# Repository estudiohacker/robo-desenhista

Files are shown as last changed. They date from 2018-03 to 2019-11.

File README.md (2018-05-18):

Projeto de um robô desenhista por [Monica Rizzolli](https://github.com/MonicaRizzolli/) e [João Adriano Freitas](https://github.com/jaafreitas/). Inspirado no [Open Source Turtle Robot ](https://github.com/aspro648/OSTR) por MakersBox.

[Vídeo demonstração](https://youtu.be/GalOWkOCb_o)

Ilustrações: Monica Rizzolli

## Lista de materiais

* 2 motores de passo 28BYJ-48 5VDC

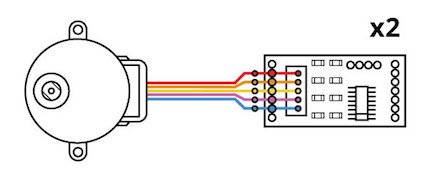
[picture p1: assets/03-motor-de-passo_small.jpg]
3-motor-de-passo_small
   

* 1 micro servo 9g SG90

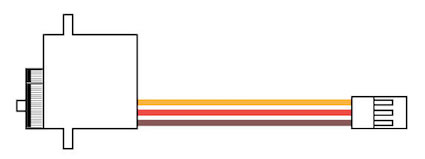
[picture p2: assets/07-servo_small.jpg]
7-serv
   

* 1 Arduino Nano

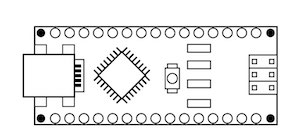
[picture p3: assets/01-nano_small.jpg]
1-nano_smal
   

* 1 Placa Shield de Expansão para Arduino Nano

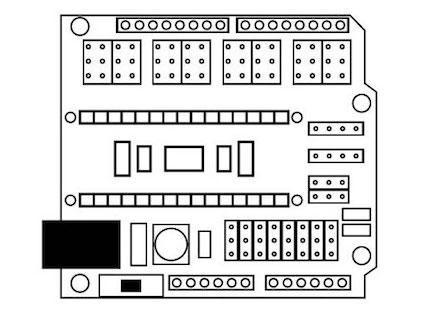
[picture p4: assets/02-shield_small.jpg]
2-shield_smal
   

* 1 Cabo USB compatível com o Arduino Nano

* 12 Jumpers fêmea-fêmea

   0-jumpers_femea_femea_smal
   
* 14 porcas fêmeas hexagonal M3
* 18 parafusos Allen M3x8
* 14 parafusos cabeça redonda M2.5x8
* 1 bola de metal 5/8"
* 2 anéis de borracha (O-ring) 1 7/8" x 1/8"

## Montagem eletrônica
* Micro servo na porta digital 2: fio laranja no S, vermlho no V e marrom no G

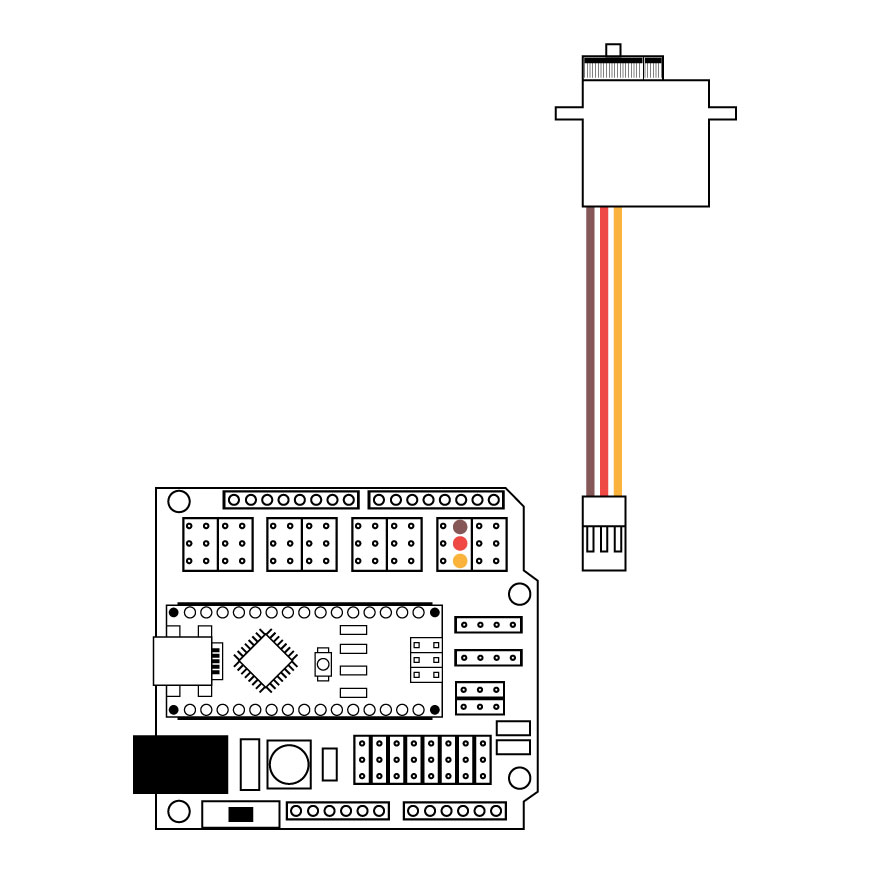
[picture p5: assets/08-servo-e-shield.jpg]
8-servo-e-shield
  

* Motor de passo da direita: pino digital S 4 no IN1, S 5 no IN2, S 6 no IN3 e S 7 no IN4. Alimentação 4 V no + e 4 G no -.

* Motor de passo da esquerda: pino digital S 8 no IN1, S 9 no IN2, S 10 no IN3 e S 11 no IN4. Alimentação 8 V no + e 4 G no -.

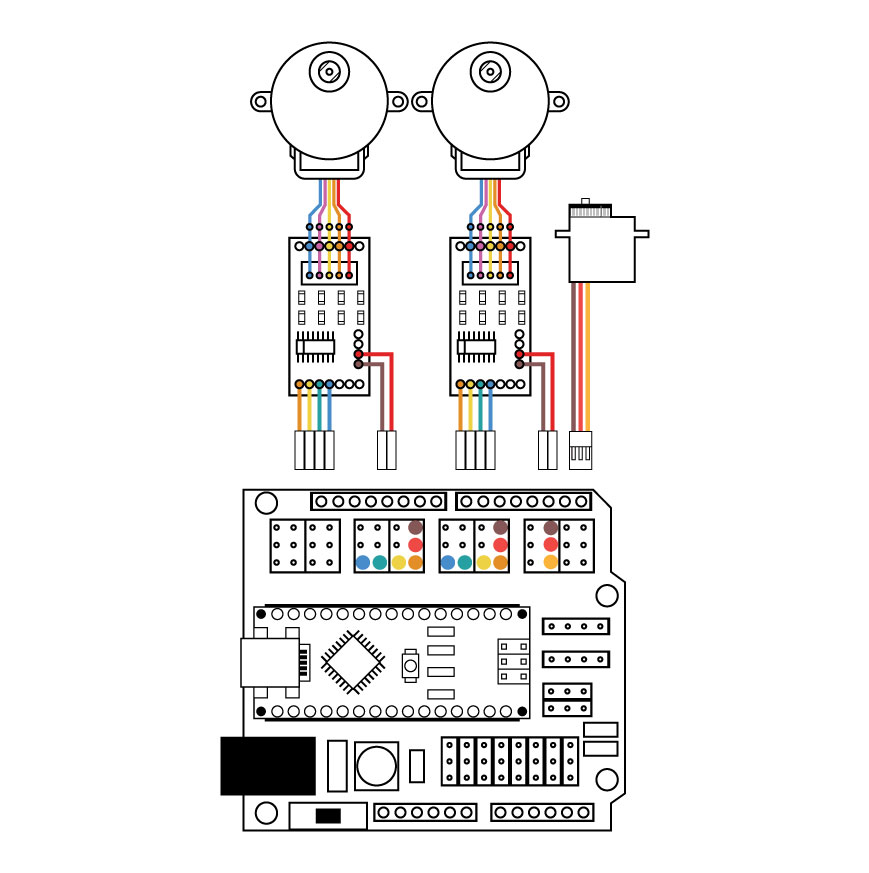
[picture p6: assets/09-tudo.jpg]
9-tud


## Licença
[Attribution-ShareAlike 3.0 United States (CC BY-SA 3.0 US)](https://creativecommons.org/licenses/by-sa/3.0/us/)

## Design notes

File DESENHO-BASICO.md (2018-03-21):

## Desenho Básico

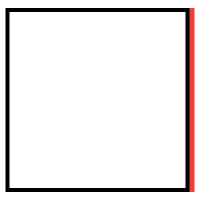
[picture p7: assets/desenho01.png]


```C
for (var count = 0; count < 4; count++){
  moveForward(100); // tamanho do lado do quadrado
  turnRight(90);
}
``` 

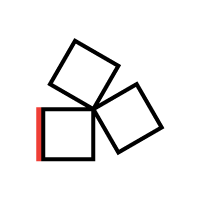
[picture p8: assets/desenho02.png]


```C
// nesse loop definimos quantas vezes o quadrado será desenhado - 3 nesse caso
for (var count1 = 0; count1 < 3; count1++){ 
  // nesse loop desenhamos os lados do quadrado
  for (var count = 0; count < 4; count++){ 
    moveForward(100); // definir o tamanho do lado do quadrado
    turnRight(90);
  }
  // aqui definimos quantos graus o quadrado deve rotacionar. 
  // para descobrir o ângulo, dividimos 360 pela quantidade de vezes que o quadrado é desenhado
  // nesse caso 360/3 = 120
  turnRight(120);
}
``` 

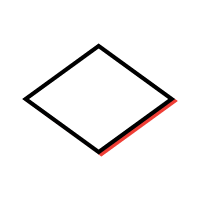
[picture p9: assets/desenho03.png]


```C
for (var count = 0; count < 2; count++){
  moveForward(100); // tamanho do lado do losango
  turnRight(60);
  moveForward(100); // tamanho do lado do losango
  turnRight(120);
}
```

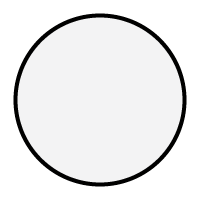
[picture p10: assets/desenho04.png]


```C
for (var count = 0; count < 360; count++){
  moveForward(1);
  turnRight(1);
}
```

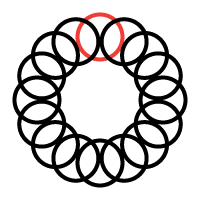
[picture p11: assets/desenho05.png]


```C
// nesse loop definimos quantas vezes o círculo será desenhado - 16 nesse caso
for (var count1 = 0; count1 < 16; count1++){
  // desenhar o círculo
  for (var count = 0; count < 360; count++){
    moveForward(1);
    turnRight(1);
  }
  jumpForward(50); // testar outros valores
  // para descobrir o ângulo, dividimos 360 pela quantidade de vezes que o quadrado é desenhado
  // nesse caso 360/16 = 22.5
  turnRight(22.5);
}
``` 

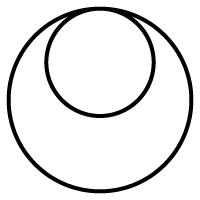
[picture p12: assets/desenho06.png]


```C
// círculo menor
for (var count = 0; count < 36; count++){
  moveForward(5);
  turnRight(10);
}

//círculo maior
for (var count = 0; count < 36; count++){
  moveForward(10);
  turnRight(10);
}
```

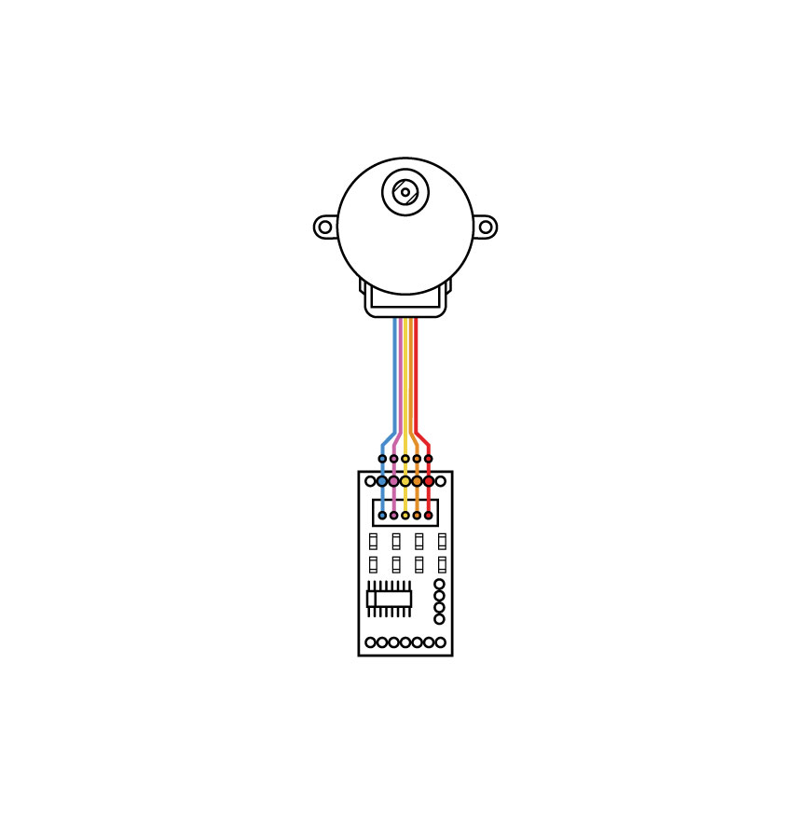
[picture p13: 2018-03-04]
assets/03-motor-de-passo.jpg

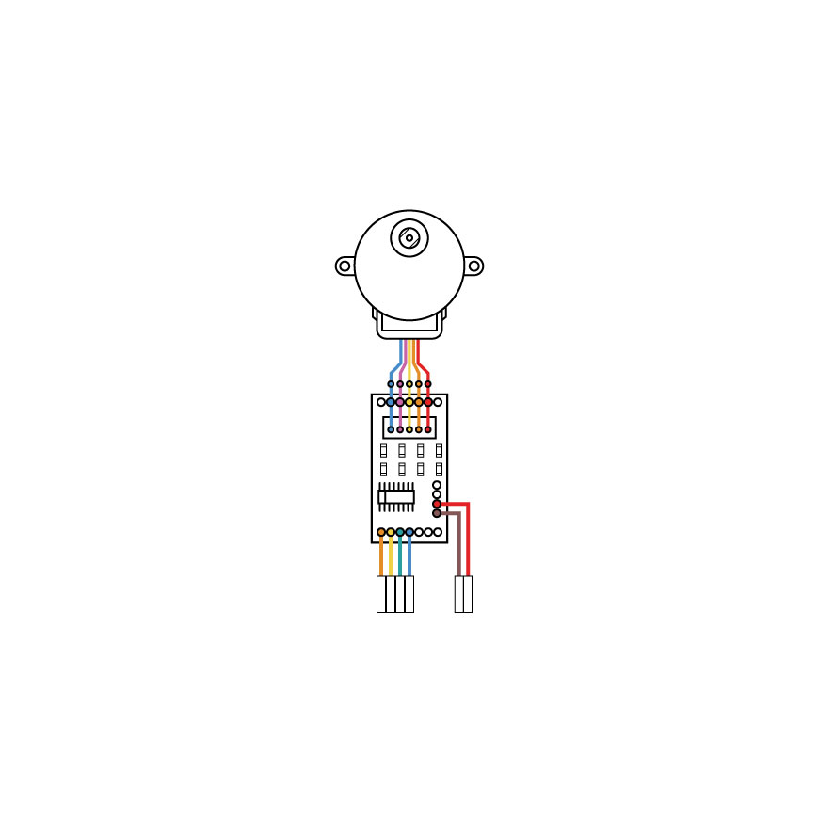
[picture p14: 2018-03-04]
assets/04-passo-com-cabos.jpg

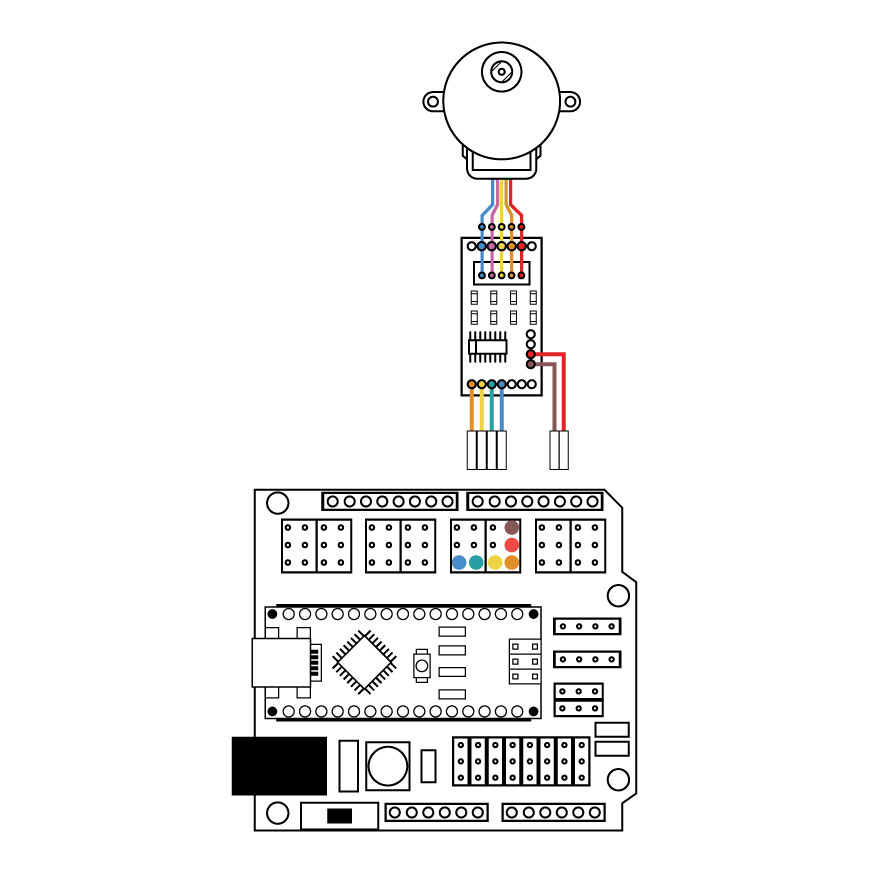
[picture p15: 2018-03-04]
assets/05-passo-com-shield.jpg

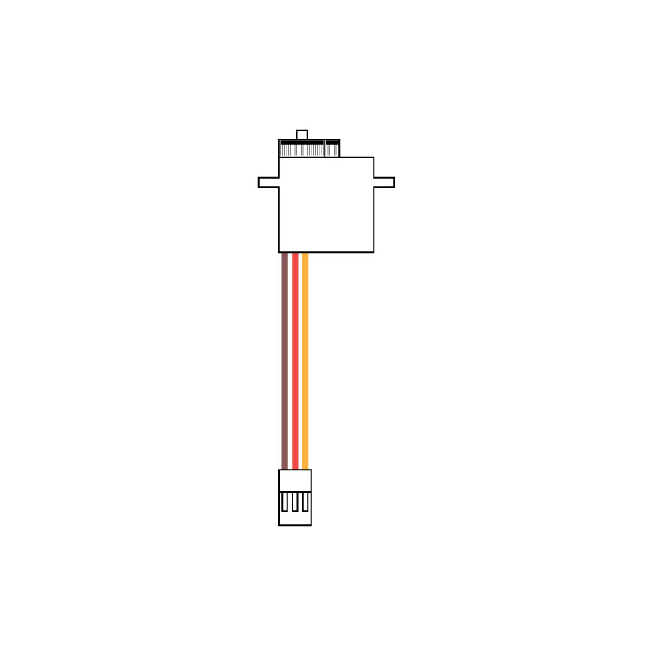
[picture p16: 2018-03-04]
assets/07-servo.jpg

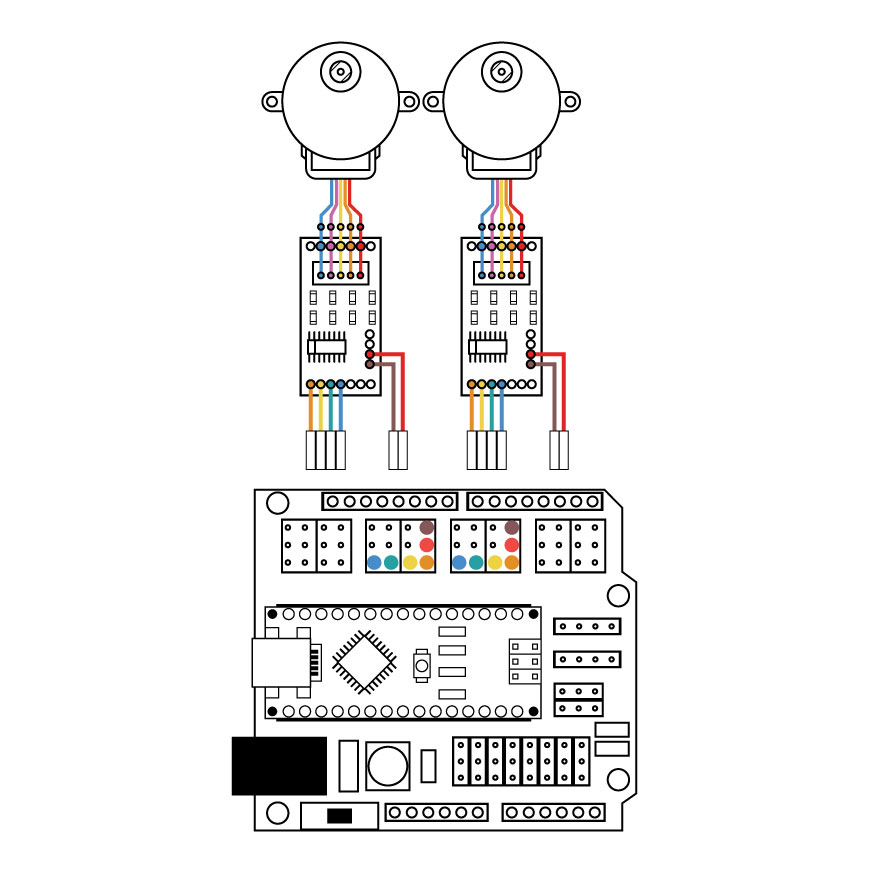
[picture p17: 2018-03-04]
assets/06-dois-motores.jpg

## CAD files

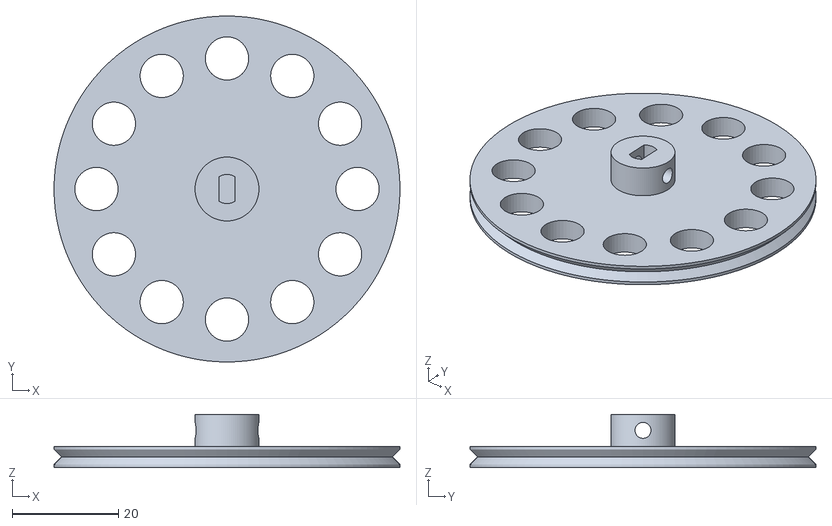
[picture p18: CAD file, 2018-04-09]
modelo/Wheel.stl
65.0 x 65.0 x 10.0

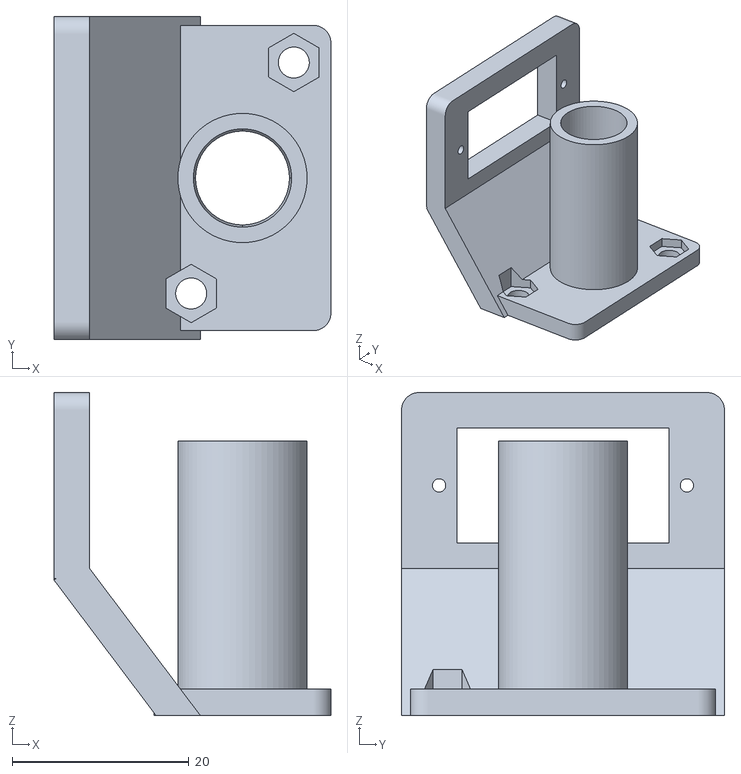
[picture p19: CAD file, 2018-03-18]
modelo/Pen_Holder2_edited.stl
31.3 x 36.5 x 36.5

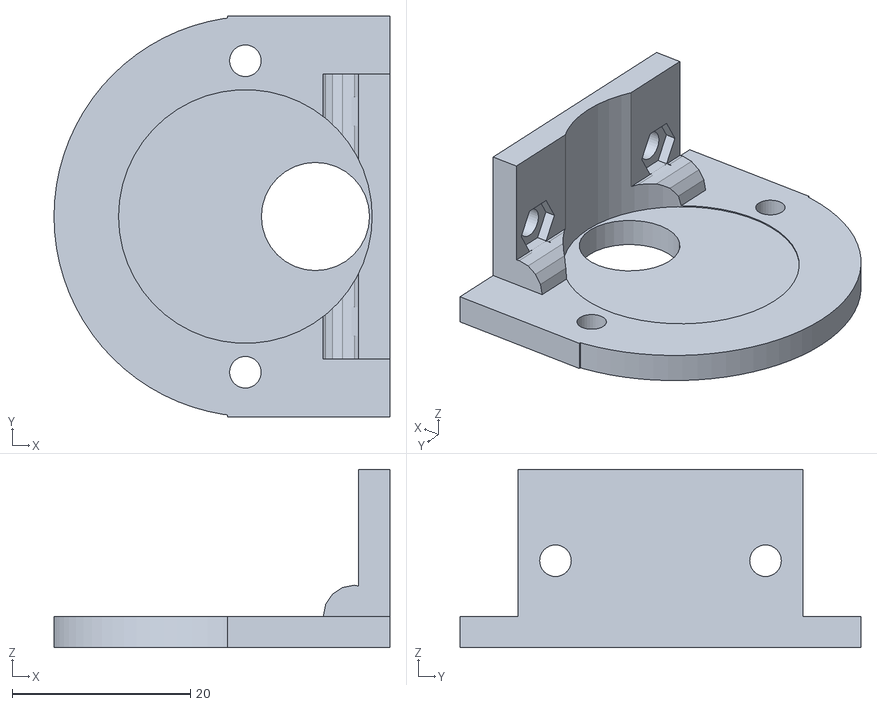
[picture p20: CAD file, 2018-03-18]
modelo/Stepper_Bracket2.stl
37.8 x 45.0 x 20.0

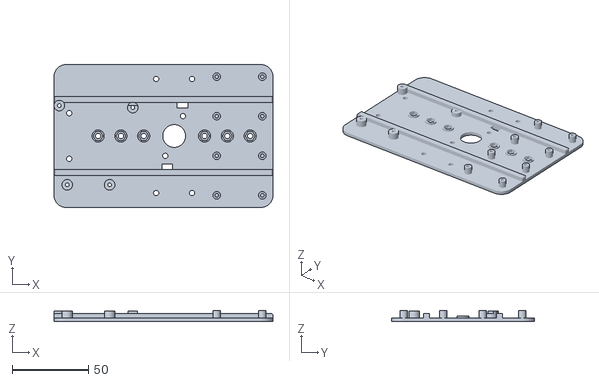
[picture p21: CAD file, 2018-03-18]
modelo/Chassis_Arduino2-modules.stl
144.0 x 94.0 x 7.40

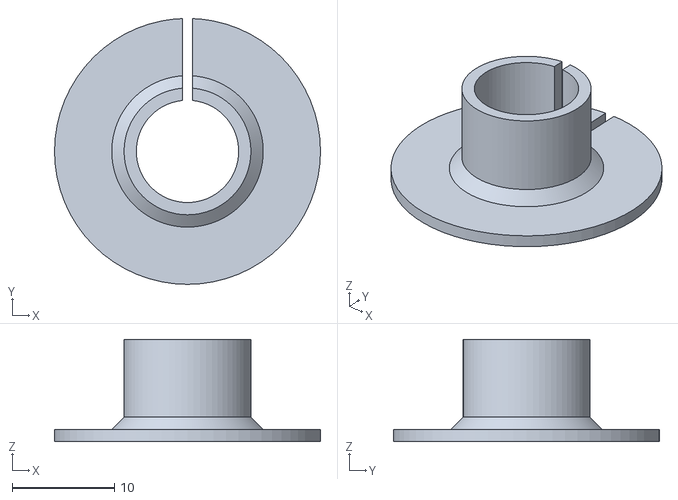
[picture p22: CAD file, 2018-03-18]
modelo/Pen_Collar2.stl
26.0 x 26.0 x 10.0

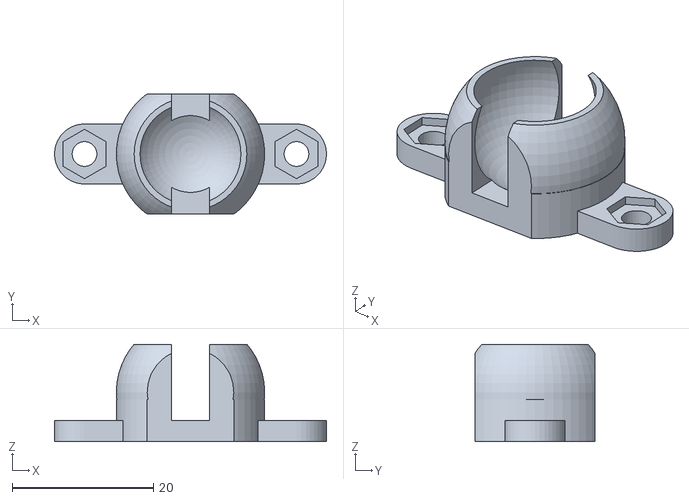
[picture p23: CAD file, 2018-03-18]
modelo/Caster2.stl
38.5 x 17.0 x 13.8

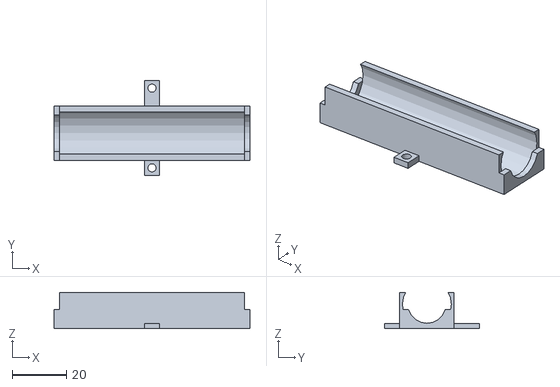
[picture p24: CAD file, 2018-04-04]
modelo/18650 battery holder.stl
72.0 x 34.8 x 13.4

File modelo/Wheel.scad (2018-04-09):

// Original script by Mark Benson
// http://www.thingverse.com/thing:122070
// 23/07/2013

// Wheel for maze mouse
// Shaft fitting for 28BYJ-48 geared stepper

// Modified by 648.ken@gmail.com Jun 2015
// Lengthened hub
// increased shaft cutout
// Included M3 set screw hole (might need to be tapped)
// Added parameters for customizer

// Creative commons non commercial


// http://www.thingiverse.com/thing:16193/
use <write/Write.scad>


/* [Global] */
features = "spokes"; // [spokes, plain, hub-only]

/* [Wheel] */
// Diameter of wheel in mm.
wheel_diameter = 65;

// Increase shaft cutout size in mm if your printer is not calibrated.
fudge_factor = 0;

/* [Text] */

// You will have to flip it around to see it. 
text = "Estudio Hacker";

// Font selection
font = "orbitron.dxf";

// 8mm goes all the way through, but may cause trouble with letters like "B".
letter_depth = 2; // [0:8]

// Letter spacing
letter_spacing = 1.3; 

// Letter height in mm.
letter_height = 6.8;


difference(){
	union()	{
		//rim
        if (features != "hub-only"){
            cylinder(r=wheel_diameter / 2, h=4, $fn=100);
        }

		//boss
		cylinder(r=12 / 2, h=10, $fn=100);
	}


	union()	{
		//shaft cutout (shaft with flat)
		translate([0, 0, 0.6])
		intersection(){
			cylinder(r=5.5 / 2 + fudge_factor, h=12, $fn=40); // was 5
			translate([0, 0, 4]) cube([3.0 + fudge_factor, 12, 12], 
                                       center=true); // was 2.5
		}

		// set screw for M3
		translate([0, 0, 7])		
		rotate([90, 0, 90])
		cylinder(r=1.5, h=60, center=true, $fn=40); // was 1

		//rim groove cutout
		translate([0, 0, 2])
		rotate_extrude(convexity=10, $fn=100)
		translate([wheel_diameter / 2, 0, 10])
		rotate([0,0,45])
		square([2,2],center=true);

        // add text to face
        if(letter_depth > 0){
            rotate(180, [1, 0, 0]){
                writecircle(text, [0, 0, 0], 
                            wheel_diameter / 3.1 - letter_height, 
                            font=font, space=letter_spacing, 
                            t=letter_depth, h=letter_height);
            }
        }
        // add spokes (circular cut-outs)        
        if (features == "spokes"){
            for(i = [0:11]){
                rotate(i * 360 / 12, [0, 0, 1])
                translate([wheel_diameter / 2.75, 0, -1])
                cylinder(r=wheel_diameter / 16, h=8, $fn=40);
            }
        }
	}
}

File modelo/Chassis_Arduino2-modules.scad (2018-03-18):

$fn = 64;


baseThickness = 2.4;
cornerRounding = 8;
plateOffset = 7;    // shift entire plate on x axis
railOffset = 16;     // plate lenght - railLength
M3holeDia = 3.5;
M3nutDia = 6.5;
holeOffset = M3holeDia * 1.2;
batteryOffset = 20;

cassis_wid = 94; // 94 for full Raspberry Pi, 84 for A+ ?
cassis_len = 144;

xArduinoOffset = 20;
yArduinoOffset = -4;

penDiameter = 15.0;
penRadius = penDiameter / 2;
baseLen = 34.5;
baseWid = 20;

railWidth = 4;

cutout_len = 45;
cutout_wid = 15;

difference(){
    
    union(){
        // cassis plate
        translate([-cassis_len / 2 - plateOffset, -cassis_wid / 2, 0])
        roundedCube(cassis_len, cassis_wid, baseThickness, cornerRounding);
        
        // rail
        translate([-cassis_len / 2 - plateOffset, 
                   cassis_wid / 2 - 25 + railWidth, baseThickness / 2])
            rotate([90, 0, 0])    
            roundedCube(cassis_len, 4, railWidth, 1);
        
        //rail
        translate([-cassis_len / 2 - plateOffset, 
                   -cassis_wid / 2 + 25, baseThickness / 2])
            rotate([90, 0, 0])    
            roundedCube(cassis_len, 4, railWidth, 1); 
     
        // Arduino mount standoffs
        rotate([0, 0, -90])
        translate([-40, -74, 0])
        union(){


        // Arduino mounts lower left (power jack)
        translate([xArduinoOffset, yArduinoOffset + 2.5, 0])
        color("lightblue")
        cylinder(standoffThickness, standoffDia / 2, standoffDia / 2);

        // upper left (USB)
        translate([xArduinoOffset + 1.3, yArduinoOffset+ (53.3 - 2.5), 0])
        color("lightblue")
        cylinder(standoffThickness, standoffDia / 2, standoffDia / 2);

        // upper right
        translate([xArduinoOffset + 1.3 + 50.8, yArduinoOffset +(53.3 - 2.5 - 15.2), 0])
        color("lightblue")
        cylinder(standoffThickness, standoffDia / 2, standoffDia / 2);

        // lower right
        translate([xArduinoOffset + 1.3 + 50.8, yArduinoOffset + (53.3 - 2.5 - 15.2 - 27.9), 0])
        color("lightblue")
        cylinder(standoffThickness, standoffDia / 2, standoffDia / 2);
        }
        
        //battery standoffs
        translate([batteryOffset, 0, baseThickness - 1])
        cylinder(baseThickness, d=standoffDia + 1, d=standoffDia + 1);  
        translate([batteryOffset + 15, 0, baseThickness - 1])
        cylinder(baseThickness, d=standoffDia + 1, d=standoffDia + 1);
        translate([batteryOffset + 30, 0, baseThickness - 1])
        cylinder(baseThickness, d=standoffDia + 1, d=standoffDia + 1);   

        translate([-batteryOffset, 0, baseThickness - 1])
        cylinder(baseThickness, d=standoffDia + 1, d=standoffDia + 1);  
        translate([-batteryOffset - 15, 0, baseThickness - 1])
        cylinder(baseThickness, d=standoffDia + 1, d=standoffDia + 1);
        translate([-batteryOffset - 30, 0, baseThickness - 1])
        cylinder(baseThickness, d=standoffDia + 1, d=standoffDia + 1);        
		
		// stepper board standoffs
 
		translate([batteryOffset+5, 12-8, baseThickness - 4])
			servo_board();
		translate([batteryOffset+5, -56+8, baseThickness - 4])
			servo_board();
    }

    // center pen hole
    cylinder(baseThickness, penRadius, penRadius);


    // pen holder bolt holes (low left, counter-clockwise)
    translate([-baseWid / 2 + holeOffset, -baseLen / 2 + holeOffset, 0])
    cylinder(baseThickness, d=M3holeDia, d=M3holeDia);
    
    /*
    translate([baseWid / 2 - holeOffset, -baseLen / 2 + holeOffset, 0])
    cylinder(baseThickness, d=M3holeDia, d=M3holeDia);
    */
    translate([baseWid / 2 - holeOffset, baseLen / 2 - holeOffset, 0])
    cylinder(baseThickness, d=M3holeDia, d=M3holeDia);
    /*
    translate([-baseWid / 2 + holeOffset, baseLen / 2 - holeOffset, 0])
    cylinder(baseThickness, d=M3holeDia, d=M3holeDia);
    */

    // bracket bolt holes
    bracketOffset = 9.5;
    translate([11.8, cassis_wid / 2 - bracketOffset, 0])
    cylinder(baseThickness, d=M3holeDia, d=M3holeDia);    

    translate([-11.8, cassis_wid / 2 - bracketOffset, 0])
    cylinder(baseThickness, d=M3holeDia, d=M3holeDia);    

    translate([11.8, -cassis_wid / 2 + bracketOffset, 0])
    cylinder(baseThickness, d=M3holeDia, d=M3holeDia);    

    translate([-11.8, -cassis_wid / 2 + bracketOffset, 0])
    cylinder(baseThickness, d=M3holeDia, d=M3holeDia);   


    // cable runs
    translate([2, 22 - M3holeDia, 0])
    cube([M3holeDia * 2, M3holeDia, baseThickness, ]); 

    translate([-8, -22, 0])
    cube([M3holeDia * 2, M3holeDia, baseThickness, ]); 
   
   
    // caster mount
    translate([-cassis_len / 2 + 10 - plateOffset, -15, 0])
    cylinder(baseThickness, d=M3holeDia, d=M3holeDia);     
    translate([-cassis_len / 2 + 10 - plateOffset, 15, 0])
    cylinder(baseThickness, d=M3holeDia, d=M3holeDia);    
  
    // battery holes
    translate([batteryOffset, 0, 0])
    cylinder(baseThickness, d=M3holeDia, d=M3holeDia);  
    translate([batteryOffset + 15, 0, 0])
    cylinder(baseThickness, d=M3holeDia, d=M3holeDia);
    translate([batteryOffset + 30, 0, 0])
    cylinder(baseThickness, d=M3holeDia, d=M3holeDia);   

    translate([-batteryOffset, 0, 0])
    cylinder(baseThickness, d=M3holeDia, d=M3holeDia);  
    translate([-batteryOffset - 15, 0, 0])
    cylinder(baseThickness, d=M3holeDia, d=M3holeDia);
    translate([-batteryOffset - 30, 0, 0])
    cylinder(baseThickness, d=M3holeDia, d=M3holeDia); 



    // battery nut nolders
    translate([batteryOffset, 0, baseThickness - 1])
    cylinder(baseThickness, d=M3nutDia, d=M3nutDia, $fn=6);
    translate([batteryOffset + 15, 0, baseThickness - 1])
    cylinder(baseThickness, d=M3nutDia, d=M3nutDia, $fn=6);
    translate([batteryOffset + 30, 0, baseThickness - 1])
    cylinder(baseThickness, d=M3nutDia, d=M3nutDia, $fn=6);   

    translate([-batteryOffset, 0, baseThickness - 1])
    cylinder(baseThickness, d=M3nutDia, d=M3nutDia, $fn=6);  
    translate([-batteryOffset - 15, 0, baseThickness - 1])
    cylinder(baseThickness, d=M3nutDia, d=M3nutDia, $fn=6);
    translate([-batteryOffset - 30, 0, baseThickness - 1])
    cylinder(baseThickness, d=M3nutDia, d=M3nutDia, $fn=6);



 
    // cutouts?
    /*
    translate([- cutout_len / 2 + 35, -cassis_wid / 2 + 25, 0])
    cube([cutout_len, cutout_wid, baseThickness]);
    translate([- cutout_len / 2 + 35, cassis_wid / 2 - 25 - cutout_wid, 0])
    cube([cutout_len, cutout_wid, baseThickness]);

    translate([-cutout_len / 2 - 35, -cassis_wid / 2 + 25, 0])
    cube([cutout_len, cutout_wid, baseThickness]);
    translate([- cutout_len / 2 - 35, cassis_wid / 2 - 25 - cutout_wid, 0])
    cube([cutout_len - 18, cutout_wid, baseThickness]);
    //translate([- cutout_len / 2 - 35, - cutout_wid / 2, 0])
    //cube([cutout_len, cutout_wid, baseThickness]);
    */


    // standoffs drills
    rotate([0, 0, -90])
    translate([-40, -74, 0])
    union(){
    // Arduino mounts lower left (power jack)
    translate([xArduinoOffset, yArduinoOffset + 2.5, 0])
    color("lightblue")
    cylinder(standoffThickness, standoffHoleDia / 2, standoffHoleDia / 2);

    // upper left (USB)
    translate([xArduinoOffset+ 1.3, yArduinoOffset + (53.3 - 2.5), 0])
    color("lightblue")
    cylinder(standoffThickness, standoffHoleDia / 2, standoffHoleDia / 2);

    // cutout for solder joints
    translate([xArduinoOffset+ 1.3 - 1.5, yArduinoOffset + (53.3 - 2.5) -standoffThickness / 2, 5.5])
    color("lightblue")
    cube(standoffThickness, standoffThickness, 8);


    // upper right
    translate([xArduinoOffset + 1.3 + 50.8 , yArduinoOffset + (53.3 - 2.5 - 15.2), 0])
    color("lightblue")
    cylinder(standoffThickness, standoffHoleDia / 2, standoffHoleDia / 2);

    // lower right
    translate([xArduinoOffset + 1.3 + 50.8, yArduinoOffset + (53.3 - 2.5 - 15.2 - 27.9), 0])
    color("lightblue")
    cylinder(standoffThickness, standoffHoleDia / 2, standoffHoleDia / 2);
    }

	
}

module stand_off()
{
    translate([0,0,-1])
    {
        difference() 
        {
            cylinder(h=5,d=5, center= false);
            cylinder(h=5,d=2.5, center= false);
        }
    }
}

module servo_board()
{
    translate([3,9,5]) stand_off();
    translate([3,35,5]) stand_off();
    translate([33,9,5]) stand_off();
    translate([33,35,5]) stand_off();
}

module roundedCube(xdim ,ydim ,zdim, rdim){
	hull(){ // https://youtu.be/gKOkJWiTgAY
		translate([rdim, rdim, 0]) cylinder(zdim, rdim, rdim);
		translate([xdim-rdim, rdim, 0]) cylinder(zdim, rdim, rdim);
		translate([rdim, ydim-rdim, 0]) cylinder(zdim, rdim, rdim);
		translate([xdim-rdim, ydim-rdim, 0]) cylinder(zdim, rdim, rdim);
	}
}

standoffDia = 7;
standoffThickness = 7;
standoffHoleDia = 2.5;


module Pi(){
    // Pi lower left 
    translate([3.5, 3.5, 0])
        color("pink")
        difference(){
            cylinder(standoffThickness, standoffDia / 2, standoffDia / 2);
            cylinder(standoffThickness, standoffHoleDia / 2, standoffHoleDia / 2);
        }
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

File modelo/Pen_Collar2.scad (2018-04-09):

// pen holder for plotting robot

$fn = 64;

// holder variables
penDiameter = 10; // 12.5mm works with Sharpie Fine
                  // 11.75 for Visa-vis
                  // 10 mm for Crayola Washables
                  // 8.3m para caneta hidrográfica lavável Happy-time (slice = 0).
penRadius = penDiameter / 2;
barrelHieght = 10;
barrelWallThickness = 3;
baseThickness = 3;
cornerRounding = 2;

hat_thickness = 1.2;

hatDiameter = 26;
slice = 1;


module penHolder(){

	difference(){
		//// lip
        cylinder(hat_thickness, hatDiameter / 2, hatDiameter / 2);
        
        // pen hole
        cylinder(baseThickness, penRadius, penRadius);
        

        // expansion slice
        translate([ -slice / 2, 0, 0])
        cube([  slice, hatDiameter, barrelHieght]);
	}

	// pen barrel
	difference(){
        // barrel

        barrel();

		// bore
		cylinder(   barrelHieght * 2, penRadius, penRadius);

        
        // expansion slice
        translate([ -slice / 2, 0, 0])
        cube([  slice, hatDiameter * 2, hatDiameter * 2]);   
	};  
}

module barrel()
        union(){{
		cylinder(	barrelHieght, 
					penRadius + hat_thickness, 
					penRadius + hat_thickness);


        rotate_extrude($fn=200)
        //rotate([90, 0, 0])
        translate([-penRadius - 2 * hat_thickness, hat_thickness, 0])
        polygon(points=[[2,2], [2,0], [0,0]]);
        }
    }
//barrel();
penHolder();

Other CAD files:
modelo/write/orbitron.dxf
modelo/Pen_Holder2_edited.scad
modelo/Caster2.scad
modelo/Stepper_Bracket2.scad
modelo/write/Write.scad

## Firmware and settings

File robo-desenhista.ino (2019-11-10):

/*
 * Versão inicial baseada em http://www.instructables.com/id/Arduino-Drawing-Robot/
 * Adaptado por Monica Rizzolli e João Adriano Freitas.
*/

#include <Wire.h>
#include <avr/sleep.h>
#include "config.h"
#include "desenho.h"
#include "hardware.h"
#include "interface.h"

// https://github.com/madhephaestus/WiiChuck
#include "src/WiiChuck/Nunchuck.h"

Nunchuck nunchuck;

void setup() {
  Serial.begin(115200);
  Serial.println("setup");

  setupEngines();
  penup();

  nunchuck.begin();
  delay(100);
}

void loop() {
  static bool isPenDown = false;
  if (nunchuck.readData()) {
    
    // Informações para depuração.
    // Se eu comento a linha abaixo, a comunicação wire fica instável...
    nunchuck.printInputs();
    
    // Se o AccelZ (ou qualquer outro) estiver em 1023 quer dizer que estamos
    // com problemas na comunicação...
    if ((nunchuck.getAccelZ() == 1023) || (nunchuck.getButtonC())) {
      Serial.println("Reiniciando a comunicação...");
      Wire.end();

      // Rotina simplificada do início da comunicação com o Wii Nunchuk.
      Wire.begin();
      Wire.beginTransmission(0x52);
      Wire.write((uint8_t)0xF0);
      Wire.write((uint8_t)0x55);
      Wire.endTransmission();
      delay(1);
  
      Wire.beginTransmission(0x52);
      Wire.write((uint8_t)0xFB);
      Wire.write((uint8_t)0x00);
      Wire.endTransmission();
      delay(1);
    }
    digitalWrite(LED_BUILTIN, HIGH);

    bool isMoving = true;
    // Os valores 210 e 40 foram escolhidos pois estão perto das extremidades do joystick.
    if (nunchuck.getJoyY() > 210) {
      moveForward(1);
    } else if (nunchuck.getJoyY() < 40) {
      moveBackward(1);
    } else if (nunchuck.getJoyX() > 210) {
      turnRight(1);              
    } else if (nunchuck.getJoyX() < 40) {
      turnLeft(1);              
    } else {
      done();
      isMoving = false;
    }

    // Quando está movendo e abaixa a caneta, da problema na comunicação com o Nunchuk.
    // A parte boa é que dessa forma, podemos abaixar a caneta, por para movimentar e
    // soltar o botão que a caneta continua baixada.
    if (!isMoving) {
      if (nunchuck.getButtonZ() && (!isPenDown)) {
        isPenDown = true;
        pendown();
      }
      if (!nunchuck.getButtonZ() && (isPenDown)) {
        isPenDown = false;
        penup();
      }
    }
  } else {
    digitalWrite(LED_BUILTIN, LOW);

    delay(5000);

    randomSeed(analogRead(0));
    int sorteio = random(1, 7);
    Serial.print("Desenho sorteado: ");

    switch (sorteio) {
      case 1:
        Serial.println("quadrados concêntricos");
        desenho_quadradosconcentricos();        
        break;
      case 2:
        Serial.println("círculos concêntricos");
        desenho_circulosconcentricos();        
        break;
      case 3:
        Serial.println("espiral quadrados");
        desenho_espiralquadrados();
        break;
      case 4:
        Serial.println("espiral círculos");
        desenho_espiralcirculos();
        break;
      case 5:
        Serial.println("espiral triângulos");
        desenho_espiraltriangulos();
        break;
      case 6:
        Serial.println("estrela");
        desenho_estrela();
        break;
      default:
        Serial.println("teste");
        teste();
    }

    Serial.println("Dormindo...");
    Serial.end();
    set_sleep_mode(SLEEP_MODE_PWR_DOWN);
    sleep_enable();
    sleep_cpu();
  }  
}

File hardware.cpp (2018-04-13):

#include "config.h"

#include "src/AccelStepper/AccelStepper.h"
#include "src/AccelStepper/MultiStepper.h"
#ifdef RF_CONTROL
#include "src/SoftRcPulseOut/SoftRcPulseOut.h"
SoftRcPulseOut penServo;
#else
#include <Servo.h>
Servo penServo;
#endif


AccelStepper rightMotor(AccelStepper::HALF4WIRE, R_stepper_pins[0], R_stepper_pins[2], R_stepper_pins[1], R_stepper_pins[3]);
AccelStepper leftMotor(AccelStepper::HALF4WIRE, L_stepper_pins[0], L_stepper_pins[2], L_stepper_pins[1], L_stepper_pins[3]);
MultiStepper motors;

void setupEngines() {
  penServo.attach(servoPin);
  
  leftMotor.setMaxSpeed(max_speed);
  rightMotor.setMaxSpeed(max_speed);
  motors.addStepper(leftMotor);
  motors.addStepper(rightMotor);
}

int step(float distance) {
  return int(distance * steps_rev / (wheel_dia * PI));
}

float distance(float degrees) {
  return wheel_base * PI * (degrees / 360.0);
}

void move(long step_left, long step_right) {
  long steps[2];
  steps[0] = step_left;
  steps[1] = step_right;
  motors.moveTo(steps);
  motors.runSpeedToPosition();
  leftMotor.setCurrentPosition(0);
  rightMotor.setCurrentPosition(0);  
}

void forward(float distance) {
  Serial.print("↑ ");  Serial.print(distance); Serial.println("mm");
  int s = step(distance);
  move(-s, s);
}

void backward(float distance) {
  Serial.print("↓ ");  Serial.print(distance); Serial.println("mm");
  int s = step(distance);
  move(s, -s);
}

void right(float degrees) {
  Serial.print("↷ "); Serial.print(degrees); Serial.println("°");
  int s = step(distance(degrees));
  move(s, s);
}

void left(float degrees) {
  Serial.print("↶ "); Serial.print(degrees); Serial.println("°");
  int s = step(distance(degrees));
  move(-s, -s);
}

void done() { // unlock stepper to save battery
  rightMotor.disableOutputs();
  leftMotor.disableOutputs();
}

void penup() {
  Serial.println("⇞");

#ifdef RF_CONTROL
  for (int pos = PEN_DOWN; pos > PEN_UP - 15; pos -= 1) {
    penServo.write(pos);
    delay(2);
    SoftRcPulseOut::refresh();
  }   
#else    
  penServo.write(PEN_UP);
#endif
  delay(100);
}

void pendown() {
  Serial.println("⇟");

#ifdef RF_CONTROL
  for (int pos = PEN_UP; pos < PEN_DOWN + 15; pos += 1) {
    penServo.write(pos);
    delay(2);
    SoftRcPulseOut::refresh();
  }
#else    
  penServo.write(PEN_DOWN);
#endif
  delay(100);
}

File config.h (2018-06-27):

#pragma once

#include <Arduino.h>

// Os servos e os Wii Nunchuk piratas só funcionam juntos com essa definição habilitada.
#define RF_CONTROL

const uint8_t servoPin = 2;
const uint8_t L_stepper_pins[] = {8, 9, 10, 11};
const uint8_t R_stepper_pins[] = {4, 5, 6, 7};

// PEN_DOWN tem que ser sempre maior que PEN_UP, caso contrário 
// verificar a lógica em pendown() e penup() quando RF_CONTROL está definido.
const int PEN_DOWN = 130; // ângulo do servo quando a caneta está abaixada.
const int PEN_UP = 90;    // ângulo do servo quando a caneta está levantada.

const float wheel_dia =  66;     // diâmetro da roda em milímetros.

// separação entre as duas rodas em milímetros.
// número maior, o ângulo fica mais fechado.
const float wheel_base = 115; 
const int steps_rev = 4096;      // número de passos do step motor 28BYJ-48.

// Velocidade máxima téorica de 16.25 rpm,
// ou seja, 4096 * 16.25 = 66560 pulsos por minuto, 
// logo 1109.33 pulsos por segundo.
const int max_speed = 500;       

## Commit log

2018-01-26 Versão inicial para testes de funcionamento do robô desenhista.
2018-01-26 Separando a arte do código de controle.
2018-03-18 Modelo 3D em OpenSCAD e versão exportada em .STL
    [Caster2.scad, Caster2.stl, Chassis_Arduino2-modules.scad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]
2018-03-18 A velocidade de 16.25 pode fazer alguns motores perderem passos. Deixando o ângulo do servo mais perto do centro.
2018-03-18 Utilização da biblioteca SoftRcPulseOut para controlar o servo e liberar o timer de 16bits. Explicações mais detalhas em config.h.
2018-04-04 Biblioteca Write.scad para OpenSCAD. http://www.thingiverse.com/thing:16193/
    [Write.scad, orbitron.dxf]
2018-04-04 Módulo de suporte para baterias 18650.
    [18650 battery holder.stl]
2018-04-04 Roda modelo 60mm
    [Wheel_60.stl]
2018-04-06 Biblioteca de comunicação com Wii NunChuk. https://github.com/madhephaestus/WiiChuck
2018-04-09 Roda com 65mm de diâmetro.
    [Pen_Collar2.scad, Wheel.scad, Wheel.stl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]
2018-04-13 Novos desenhos: 7 círculos concêntricos e bandeira do brasil. Sorteio de um desenho.
2018-05-18 Completando a lista de materiais
2018-06-27 Deixando mais claro a função de cada arquivo no projeto. comandos_basicos -> interface. helper_funcions -> hardware.
2019-11-10 Colocando o arduino para dormir.
